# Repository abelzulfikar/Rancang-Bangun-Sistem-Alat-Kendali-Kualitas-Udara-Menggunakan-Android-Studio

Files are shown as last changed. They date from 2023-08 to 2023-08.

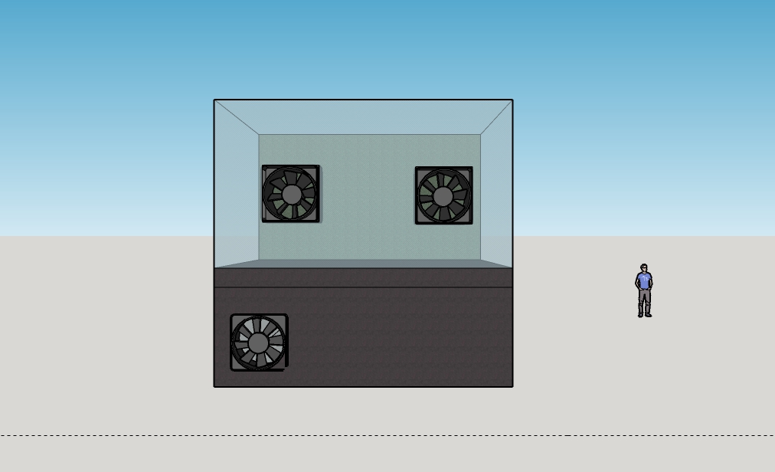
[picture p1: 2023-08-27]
Pendukung/SketchUp/bagian 2 tampilan belakang.jpg

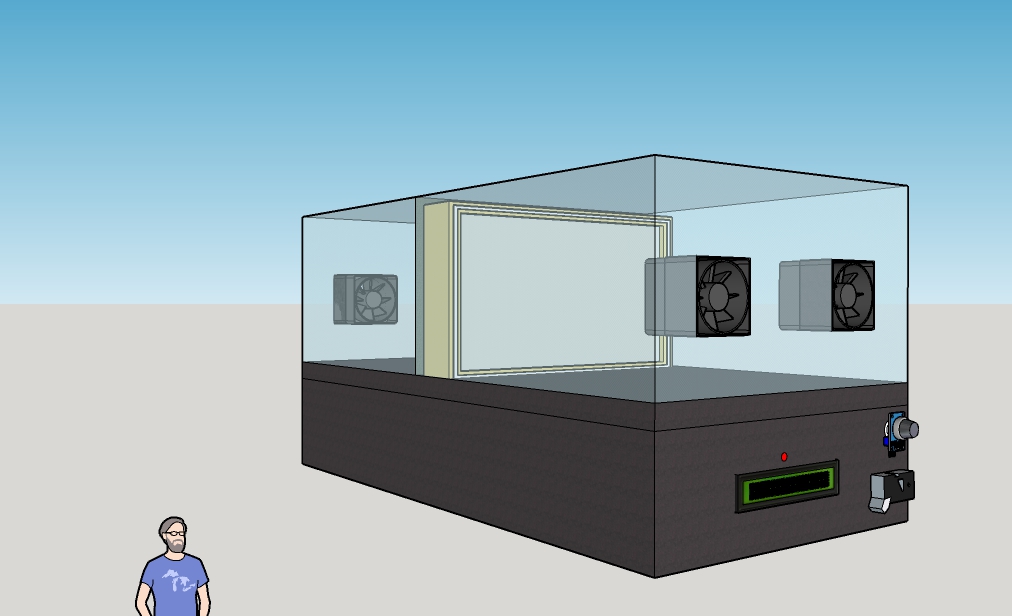
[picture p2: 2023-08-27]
Pendukung/SketchUp/bagian 2 tampilan samping 2.jpg

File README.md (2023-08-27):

# Rancang-Bangun-Sistem-Alat-Kendali-Kualitas-Udara-Menggunakan-Android-Studio
memantau dan mengatur kualitas udara dalam ruangan melalui aplikasi Android

Latar Belakang
Kualitas udara dalam ruangan memiliki dampak besar pada kesehatan dan kenyamanan manusia sehari-hari. Udara yang tercemar dapat menyebabkan gangguan pernapasan, alergi, dan dampak negatif lainnya. Karena banyaknya waktu yang dihabiskan di dalam ruangan, baik di tempat tinggal maupun tempat kerja, pengendalian kualitas udara menjadi penting. Diperlukan alat Sistem Kendali Kualitas Udara dengan sensor MQ 135 untuk mendeteksi udara tidak sehat, sensor GP2Y1010AU0F untuk sensitivitas debu, dan penambahan filter H13 atau HEPA untuk menyaring udara dari kotoran

Menghubungkan alat melalui socket AC ke sumber listrik.
1. Menghubungkan ESP 32 dengan jaringan Wi-Fi yang memiliki akses internet
2. Buka aplikasi "Freshism" yang sudah diinstal pada smartphone
3. Sensor akan membaca nilai udara dan debu dan hasilnya akan tampil di aplikasi
4. Tekan Tombol ON untuk mengaktifkan Kipas DC
5. Pilih Mode "Auto" pada tombol aplikasi "Freshism"
6. jika indikator kualitas udara tidak sehat, maka indikator led akan berwarna merah, tampilan aplikasi tidak sehat, dan kipas dc menyala

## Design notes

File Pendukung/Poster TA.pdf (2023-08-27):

PERALATAN

LATAR BELAKANG

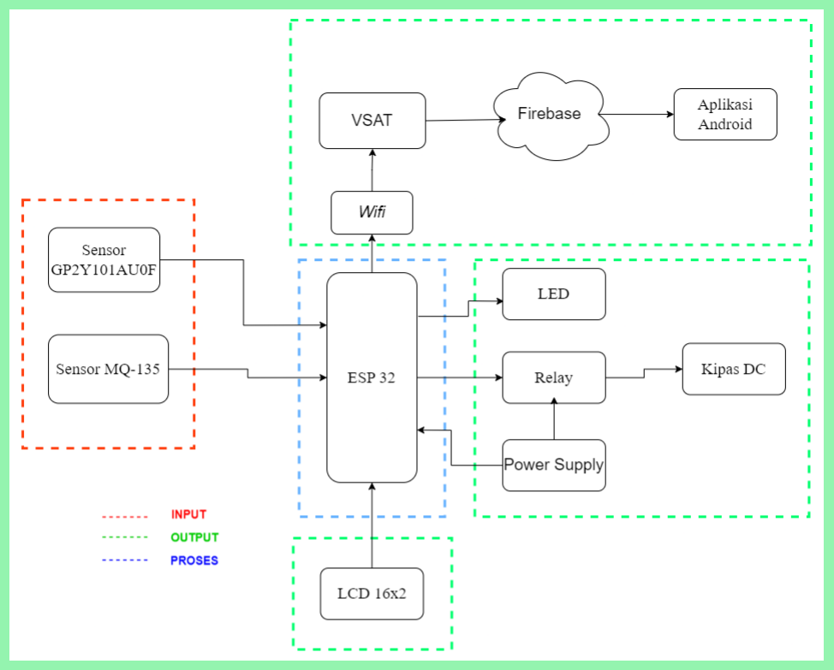
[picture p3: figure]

Rosnabila Enggar Pawening
2003332064

Pembimbing: Dita Indra Febriyanti S.Pd., M.Han NIP: 199402022022032015

NAMA MAHASISWA 2

Zulfikar Bella Ali
NIM: 2003332007

Pembimbing: Ir. Sri Danaryani., M.T. NIP: 196305031991032001

NAMA MAHASISWA 1

TUJUAN

DIAGRAM BLOK

KEMENTRIAN RISET, TEKNOLOGI, DAN PENDIDIKAN TINGGI POLITEKNIK NEGERI JAKARTA
JURUSAN TEKNIK ELEKTRO
Jl. Prof. DR. G.A. Siwabessy, Kampus UI, Depok 16425 Telp/Fax Elektro: ( 021 ) 7863531, ( 021 ) 7270036 Hunting Laman: http://www.pnj.ac.id, e-mail: elektro@pnj.ac.id

## RANCANG BANGUN SISTEM KENDALI KUALITAS UDARA MENGGUNAKAN APLIKASI ANDROID

ESP 32
Sensor MQ-135
Sensor GP2Y1010AU0F
LED RGB
Relay dua channel
LCD 16x2
Kipas DC
Power Supply

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
Kualitas udara dalam ruangan memiliki dampak besar pada kesehatan dan kenyamanan manusia
sehari-hari. | Udara | yang | tercemar | dapat
menyebabkan gangguan pernapasan, alergi, dan dampak negatif lainnya. Karena banyaknya waktu yang dihabiskan di dalam ruangan, baik di tempat tinggal maupun tempat kerja, pengendalian kualitas udara menjadi penting. Diperlukan alat Sistem Kendali Kualitas Udara dengan sensor MQ 135 untuk mendeteksi udara tidak sehat, sensor GP2Y1010AU0F untuk sensitivitas debu, dan penambahan filter H13 atau HEPA untuk menyaring udara dari kotoran

Mampu merancang catu daya dari sistem kendali kualitas udara menggunakan aplikasi Mampu untuk melakukan perancangan sistem untuk kendali kualitas udara
Mampu melakukan pengujian komponen dan pembacaan data kualitas udara dari alat kendali kualitas udara menggunakan aplikasi Mampu merancang aplikasi android sistem kendali kualitas udara.
Mampu untuk melakukan pengintergrasian antara alat sistem kendali kualitas udara dan aplikasi melalui data firebase
Mampu melakukan pengujian pembacaan data dari alat ke aplikasi

1.

2.

3.

4.

5.

6.

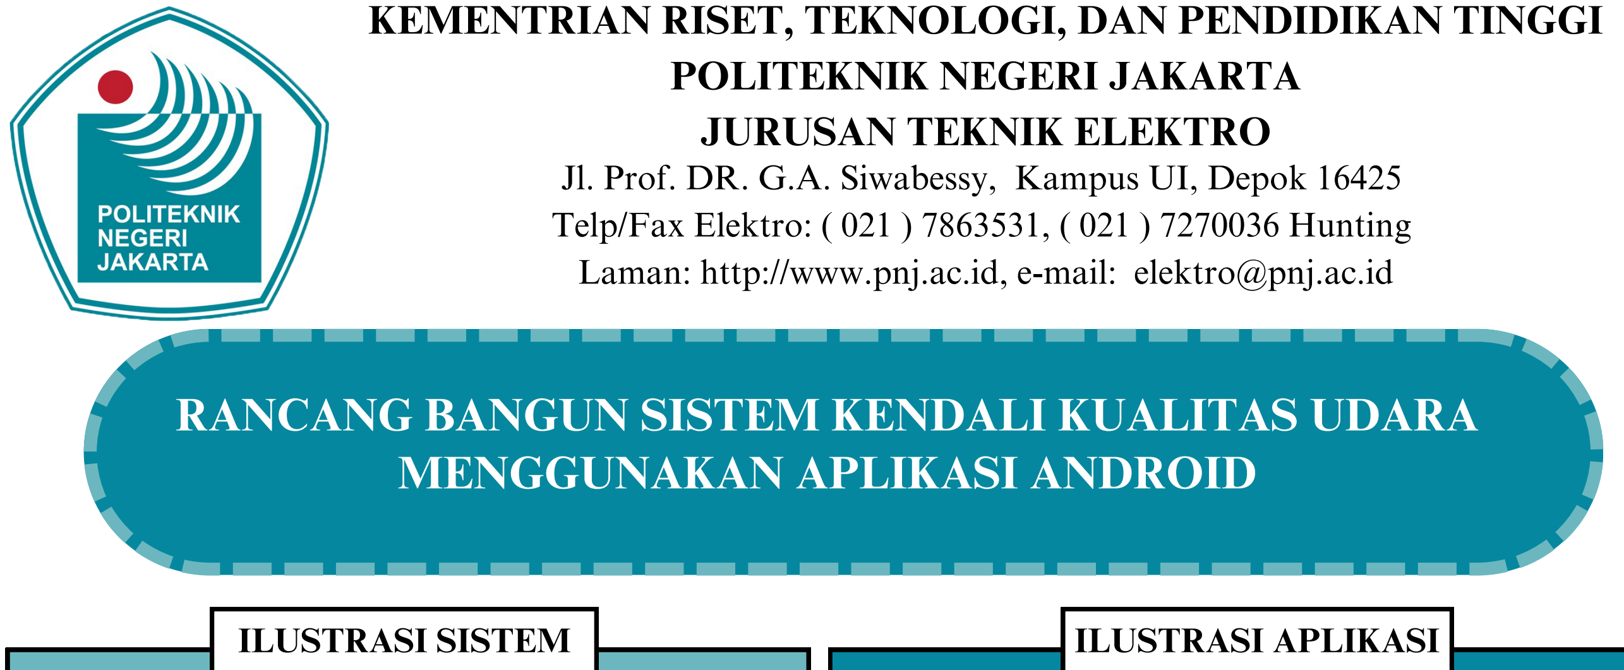
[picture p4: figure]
ILUSTRASI SISTEM; ILUSTRASI APLIKASI; POLITEKNIK NEGERI JAKARTA JURUSAN TEKNIK ELEKTRO; Laman: http://www.pnj.ac.id, e-mail: elektro@pnj.ac.id; MENGGUNAKAN APLIKASI ANDROID
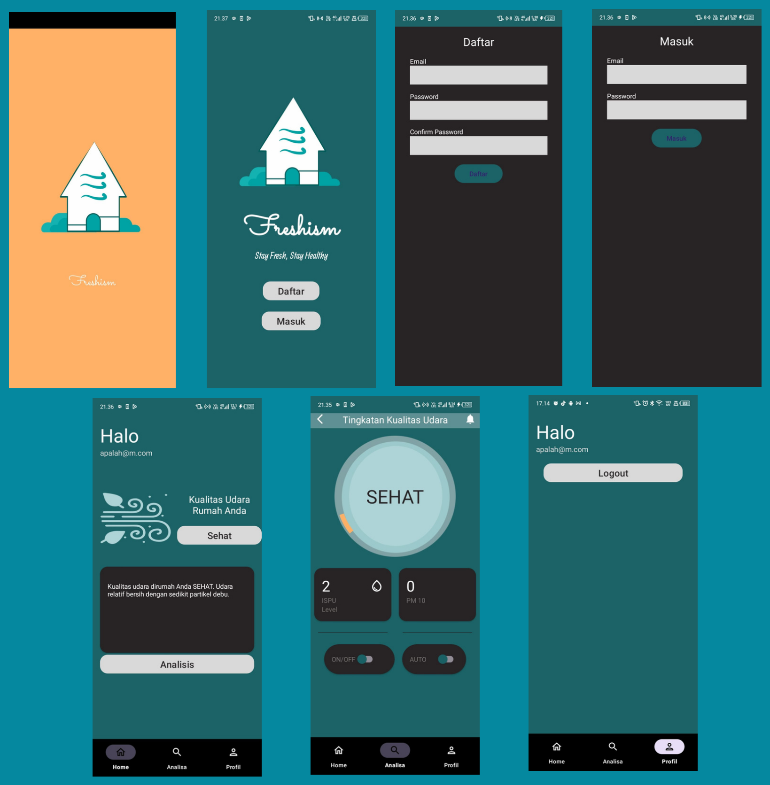
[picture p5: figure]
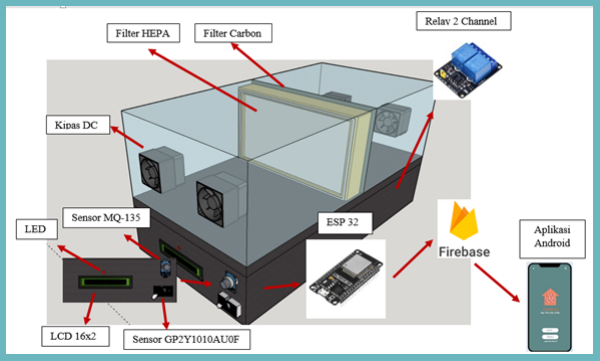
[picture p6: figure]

CARA PENGOPERASIAN ALAT

Rosnabila Enggar Pawening
NIM: 2003332064

Pembimbing: Dita Indra Febriyanti S.Pd., M.Han NIP: 199402022022032015

NAMA MAHASISWA 2

Zulfikar Bella Ali
NIM: 2003332007

Pembimbing: Ir. Sri Danaryani., M.T. NIP: 196305031991032001

NAMA MAHASISWA 1

KEMENTRIAN RISET, TEKNOLOGI, DAN PENDIDIKAN TINGGI

Jl. Prof. DR. G.A. Siwabessy, Kampus UI, Depok 16425 Telp/Fax Elektro: ( 021 ) 7863531, ( 021 ) 7270036 Hunting

## RANCANG BANGUN SISTEM KENDALI KUALITAS UDARA

Menghubungkan alat melalui socket AC ke sumber listrik.
Menghubungkan ESP 32 dengan jaringan Wi-Fi yang memiliki akses internet Buka aplikasi "Freshism" yang sudah diinstal pada smartphone
Sensor akan membaca nilai udara dan debu dan hasilnya akan tampil di aplikasi
Tekan Tombol ON untuk mengaktifkan Kipas DC
Pilih Mode "Auto" pada tombol aplikasi "Freshism"
jika indikator kualitas udara tidak sehat, maka indikator led akan berwarna merah, tampilan aplikasi tidak sehat, dan kipas dc menyala

1.
2.
3.
4.
5.
6.
7.

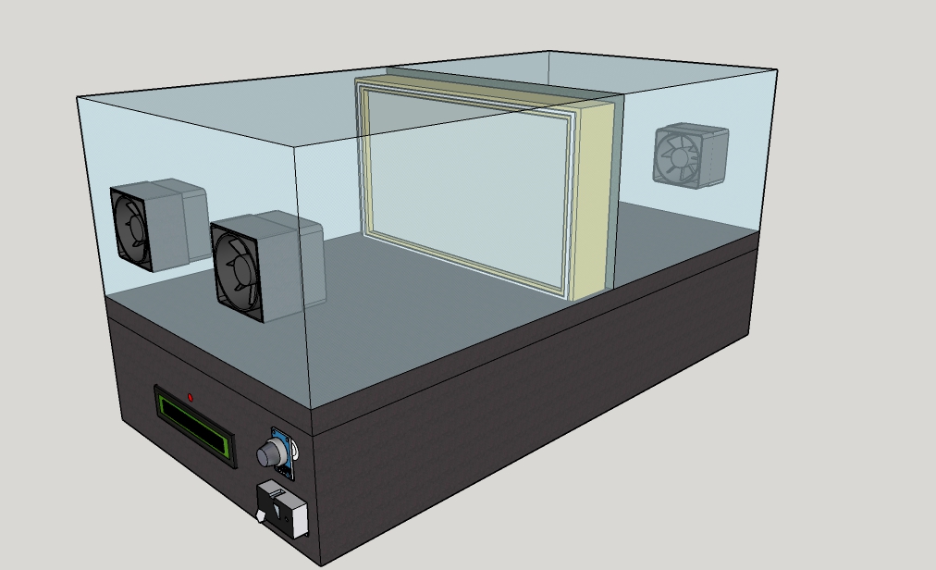
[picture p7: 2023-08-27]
Pendukung/SketchUp/bagian 2 tampilan samping.jpg

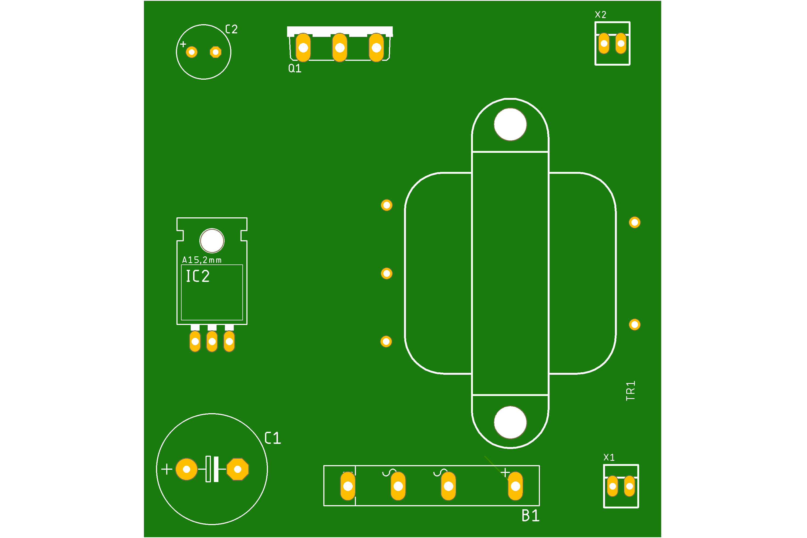
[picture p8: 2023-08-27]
Pendukung/Eagle/Power Supply untuk IC Regulator/Final.png

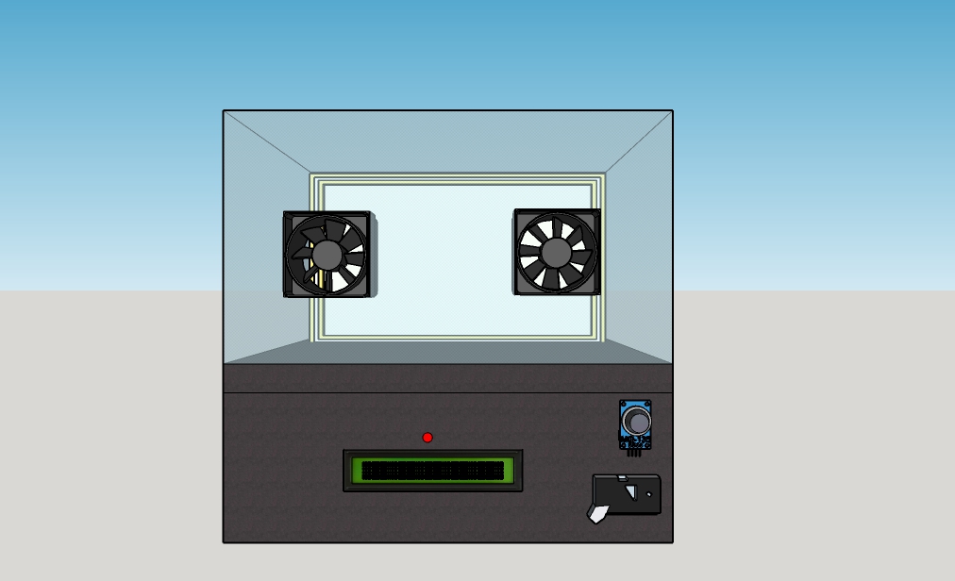
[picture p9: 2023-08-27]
Pendukung/SketchUp/bagian 2 tampilan depan.jpg

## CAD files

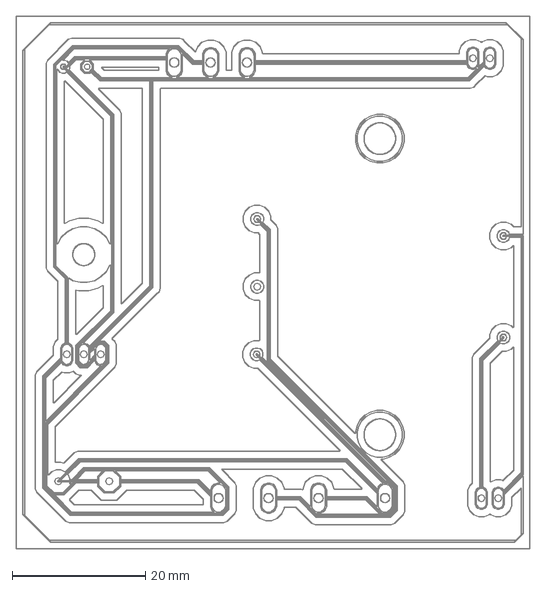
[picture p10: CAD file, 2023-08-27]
Pendukung/Eagle/Power Supply untuk IC Regulator/Final.dxf
77.1 x 80.0 mm

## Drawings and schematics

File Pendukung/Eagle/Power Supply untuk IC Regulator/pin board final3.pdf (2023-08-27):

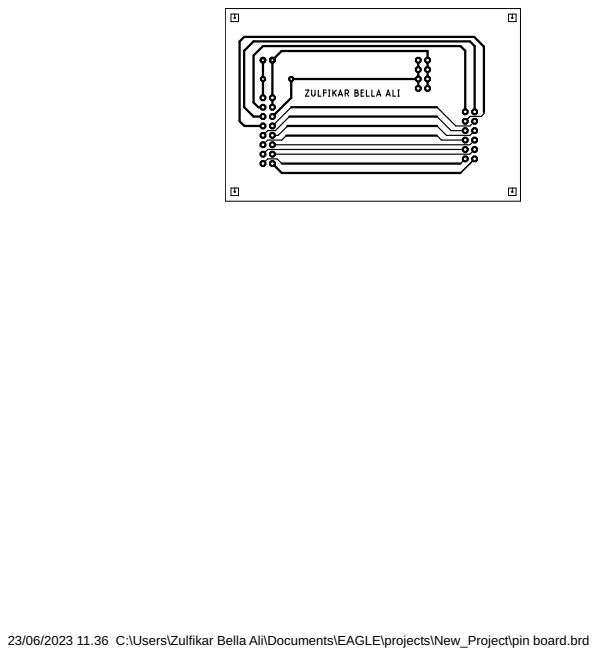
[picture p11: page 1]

23/06/2023 11.36 C:\Users\Zulfikar Bella Ali\Documents\EAGLE\projects\New_Project\pin board.brd

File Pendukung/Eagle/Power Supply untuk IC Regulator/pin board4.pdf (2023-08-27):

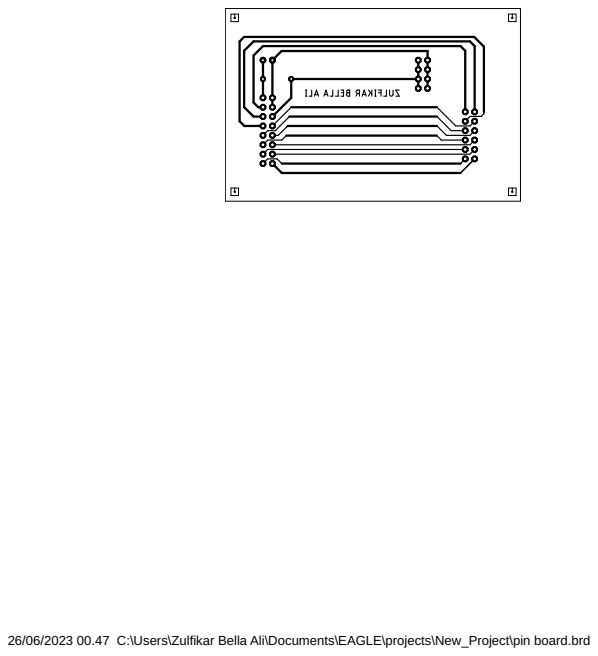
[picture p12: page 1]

26/06/2023 00.47 C:\Users\Zulfikar Bella Ali\Documents\EAGLE\projects\New_Project\pin board.brd

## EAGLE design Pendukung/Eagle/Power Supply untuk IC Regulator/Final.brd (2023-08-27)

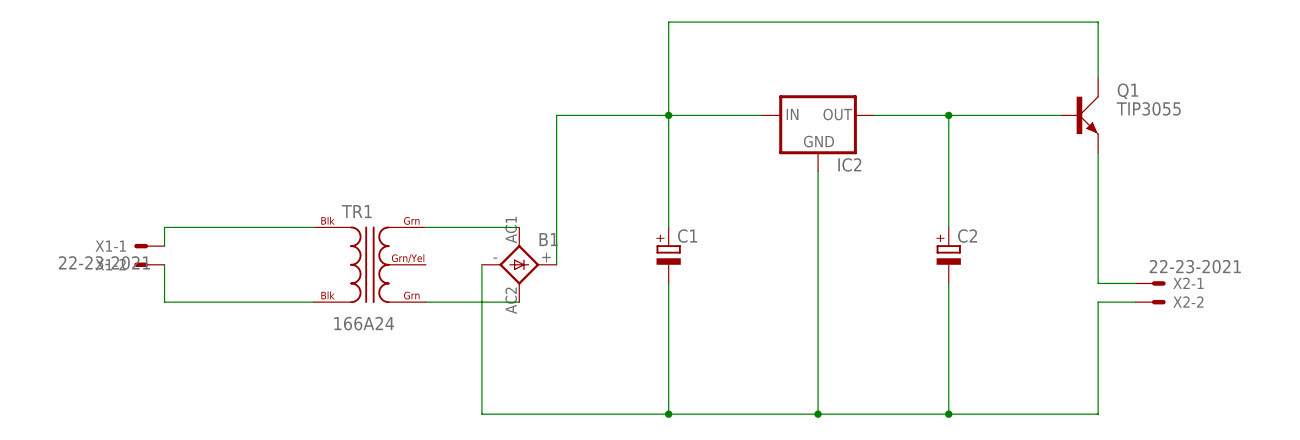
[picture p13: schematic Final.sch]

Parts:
B1: FB32
C1: CPOL-EUE7.5-16; E7,5-16
C2: CPOL-EUE3.5-8; E3,5-8
IC2: 78XXL
Q1: TIP3055; TOP3AV
TR1: 166A24; C2H
X1, X2: 22-23-2021

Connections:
unnamed: TR1.BLK@1 (BLK), X1.1
unnamed: TR1.BLK@2 (BLK), X1.2
unnamed: B1.AC1, TR1.GRN@1 (GRN)
unnamed: B1.AC2, TR1.GRN@2 (GRN)
unnamed: B1.+, C1.+, IC2.IN, Q1.C
unnamed: B1.-, C1.-, C2.-, IC2.GND, X2.2
unnamed: Q1.E, X2.1
unnamed: C2.+, IC2.OUT, Q1.B

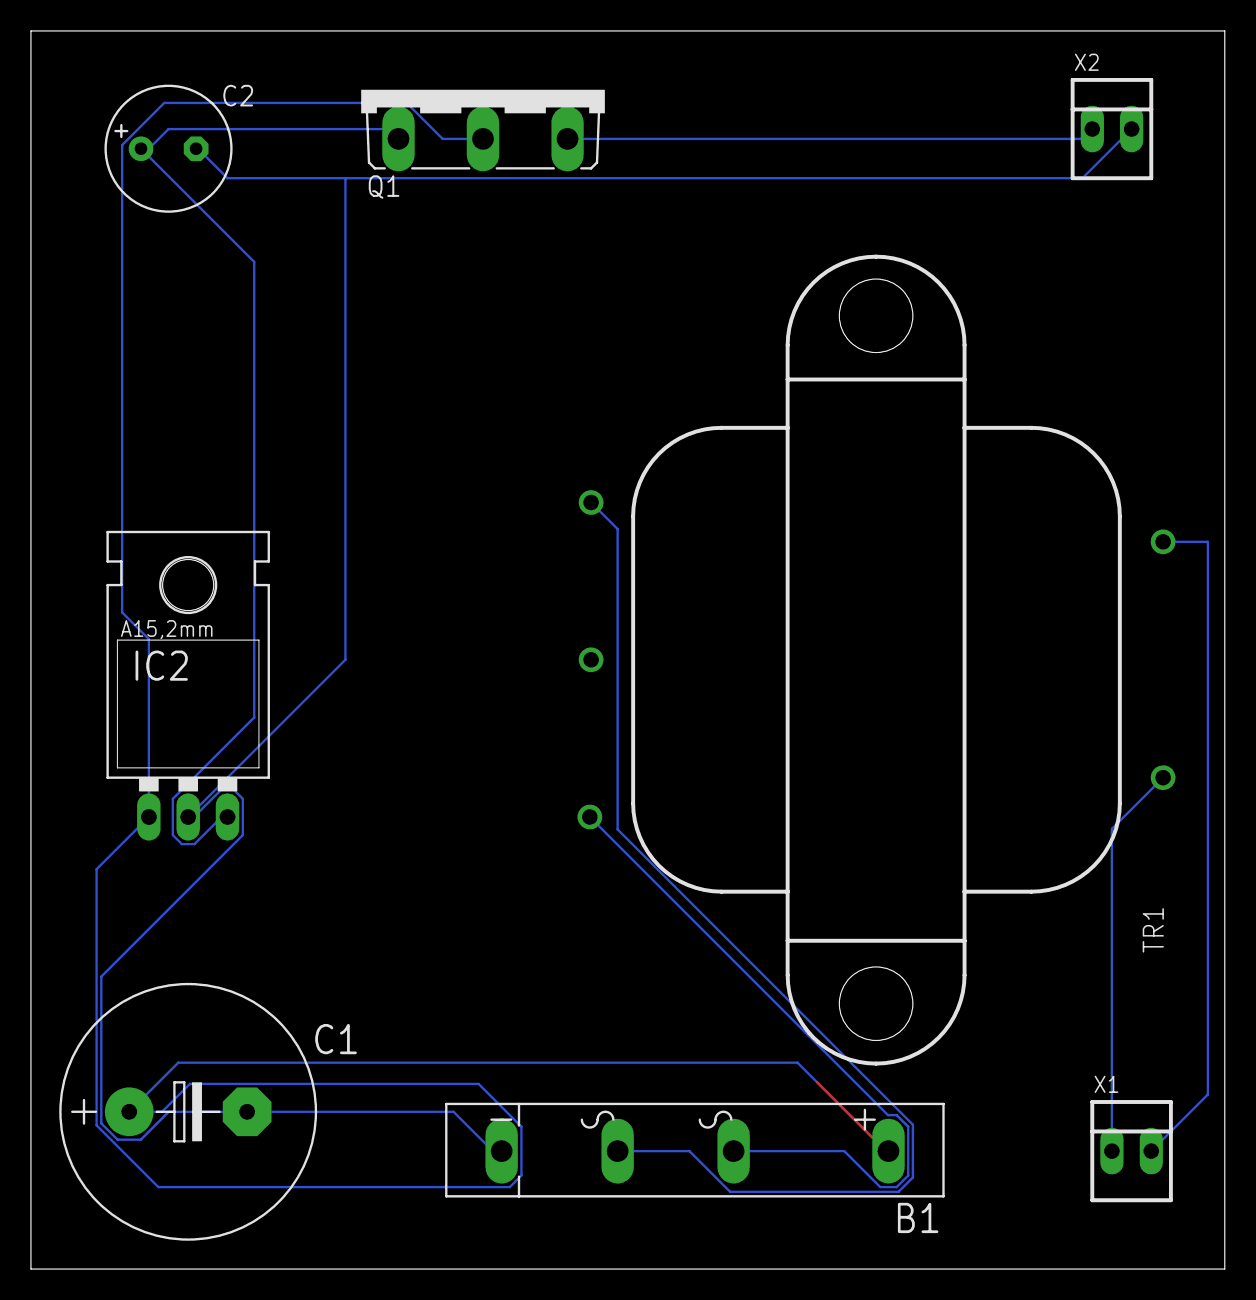
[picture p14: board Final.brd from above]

Board: 2 copper layers, 77.1 x 80.0 mm, 8 parts (0 on the bottom side), 8 nets.

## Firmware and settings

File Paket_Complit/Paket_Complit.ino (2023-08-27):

//Include the library
#include <MQUnifiedsensor.h>
#include <LiquidCrystal_I2C.h>
#include <Wire.h>

//Definitions
#define placa "ESP-32"
#define Voltage_Resolution 3.3
#define pin 35 //Analog input 0 of your arduino
#define type "MQ-135" //MQ135
#define ADC_Bit_Resolution 12 // For ESP32
#define RatioMQ135CleanAir 3.6//RS / R0 = 3.6 ppm  

const int pinGP2Y = 34;
int pinLED = 27;
int samplingTime = 280;
int deltaTime = 40;
int sleepTime = 9680;

//Declare Sensor
MQUnifiedsensor MQ135(placa, Voltage_Resolution, ADC_Bit_Resolution, pin, type);

char jenisgas[6][10] = {"CO","Alcohol","CO2","Toluen","NH4","Aceton"};
float gasA [6] = {605.18 , 77.255 , 110.47 , 44.947 , 102.2 , 34.668};
float gasB [10] = {-3.937 , -3.18 , -2.862 , -3.445 , -2.473 , -3.369};
int CO = 0;

#define relaypin 5
 
LiquidCrystal_I2C lcd(0x27,16,2);
 

 
byte pic_termo[8] = //icon for termometer
{
  B00000,
  B00000,
  B00000,
  B00000,
  B00000,
  B11111,
  B11111,
  B00000
};
 
byte pic_humd[8] = //icon for water droplet
{
    B00000,
  B00010,
  B00101,
  B01000,
  B10100,
  B00010,
  B00101,
  B00000
};
 
byte lonceng[8] = {
  B00100,
  B01110,
  B01110,
  B01110,
  B11111,
  B00000,
  B00100,
  B00000
};
 
byte lonceng1[8] = {
  B11011,
  B10001,
  B10001,
  B10001,
  B10001,
  B00000,
  B11111,
  B11011
};

void setup() {
  //Init the serial port communication - to debug the library
  Serial.begin(115200); //Init serial port
  pinMode(relaypin, OUTPUT);
  pinMode(pinLED,OUTPUT);
  
  //Set math model to calculate the PPM concentration and the value of constants
  MQ135.setRegressionMethod(1); //_PPM =  a*ratio^b
  MQ135.setA(gasA[CO]); MQ135.setB(gasB[CO]); // Configure the equation to to calculate CO concentration
  /*
    Exponential regression:
  GAS      | a      | b
  CO       | 605.18 | -3.937  
  Alcohol  | 77.255 | -3.18 
  CO2      | 110.47 | -2.862
  Toluen  | 44.947 | -3.445
  NH4      | 102.2  | -2.473
  Aceton  | 34.668 | -3.369
  */
  
  /*****************************  MQ Init ********************************************/ 
  //Remarks: Configure the pin of arduino as input.
  /************************************************************************************/ 
  MQ135.init(); 
  /* 
    //If the RL value is different from 10K please assign your RL value with the following method:
    MQ135.setRL(10);
  */
  /*****************************  MQ CAlibration ********************************************/ 
  // Explanation: 
   // In this routine the sensor will measure the resistance of the sensor supposedly before being pre-heated
  // and on clean air (Calibration conditions), setting up R0 value.
  // We recomend executing this routine only on setup in laboratory conditions.
  // This routine does not need to be executed on each restart, you can load your R0 value from eeprom.
  // Acknowledgements: https://jayconsystems.com/blog/understanding-a-gas-sensor
  Serial.print("Calibrating please wait.");
  float calcR0 = 0;
  for(int i = 1; i<=10; i ++)
  {
    MQ135.update(); // Update data, the arduino will read the voltage from the analog pin
    calcR0 += MQ135.calibrate(RatioMQ135CleanAir);
    Serial.print(".");
  }
  MQ135.setR0(calcR0/10);
  Serial.println("  done!.");
  
  if(isinf(calcR0)) {Serial.println("Warning: Conection issue, R0 is infinite (Open circuit detected) please check your wiring and supply"); while(1);}
  if(calcR0 == 0){Serial.println("Warning: Conection issue found, R0 is zero (Analog pin shorts to ground) please check your wiring and supply"); while(1);}
  /*****************************  MQ CAlibration ********************************************/ 
  MQ135.serialDebug(false);


  
  lcd.begin();
  lcd.setBacklight(255);
  lcd.setCursor(00,00);
  lcd.print("Kendali Kualitas");
  lcd.setCursor(00,1);
  lcd.print("     Udara ");
  delay(1000);
  lcd.clear();
  lcd.setCursor(00,00);
  lcd.print("Zulfikar Bella A");
  lcd.setCursor(00,1);
  lcd.print("Rosnabila Enggar");
  delay(2000);
  lcd.clear();
  lcd.createChar(1,pic_termo);
  lcd.createChar(2,pic_humd);
  lcd.createChar(3,lonceng);
  lcd.createChar(4,lonceng1);
}

void loop() {
  delay(1000);
  MQ135.update(); // Update data, the arduino will read the voltage from the analog pin
  float Udara = MQ135.readSensor(); // Sensor will read PPM concentration using the model, a and b values set previously or from the setup

  Serial.print(jenisgas[CO]);Serial.print (" : ");Serial.print(Udara);Serial.println(" ppm");
  MQ135.serialDebug(); // Will print the table on the serial port
  MQ135.init(); 

  digitalWrite(pinLED,LOW); // Turn On the LED
  delayMicroseconds(samplingTime);
  
  float voMeasured = analogRead(pinGP2Y); // Read the dust value
  delayMicroseconds(deltaTime);
  
  digitalWrite(pinLED,HIGH); // Turn Off the LED
  delayMicroseconds(sleepTime);
  
  float calcVoltage = voMeasured * (3.3/4096);
  // linear equation taken from http://www.howmuchsnow.com/arduino/airquality/
  // Chris Nafis (c) 2012
  float dustDensity = (0.17 * calcVoltage - 0.1)*1000;
  if (dustDensity < 0){
    dustDensity = 0;
  }
  Serial.print("Raw signal value (0-4045): "); Serial.print(voMeasured);
  Serial.print(" - Voltage: "); Serial.print(calcVoltage);
  Serial.print(" - Density : "); Serial.println(dustDensity);



  lcd.setCursor (00,00);
  lcd.print("UDARA  &  DEBU");
  lcd.setCursor (00,1);
  lcd.write(1);
  lcd.setCursor (1,1);
  lcd.print(Udara);

  lcd.setCursor (5,1);
  lcd.print("       ");
  lcd.setCursor (14,1);
  lcd.print("  ");
  
  lcd.setCursor (9,1);
  lcd.write(2);
  lcd.setCursor (10,1);
  lcd.print(dustDensity);

  if (Udara >= 101 ){
    lcd.clear();
    while(1){
      // Menghitung Level AQI berdasarkan nilai ppm CO2
      MQ135.setRegressionMethod(1); //_PPM =  a*ratio^b
      MQ135.setA(605.18); MQ135.setB(-3.937);
      MQ135.update(); // Update data, the arduino will read the voltage from the analog pin
  float DataUdara = MQ135.readSensor(); // Sensor will read PPM concentration using the model, a and b values set previously or from the setup

      digitalWrite(relaypin, HIGH); 
      delay(3000);
      lcd.setCursor (00,00);
      lcd.write(1);
      lcd.print(" Tidak Sehat");
      
      lcd.setCursor (1,1);
      lcd.print(DataUdara);
      lcd.setCursor (5,1);
      lcd.print("      ");
      lcd.setCursor (9,1);
      lcd.print("FAN ON");
      
      lcd.setCursor (8,1);
      lcd.write(3);
      delay(2000);
      lcd.setCursor (8,1);
      lcd.write(4);
      delay(2000);
 
      
      if (DataUdara <= 100) {
        digitalWrite(relaypin, LOW); 
        lcd.clear();
        break;
        }
    }
  }

  if (dustDensity >= 101 ){
    lcd.clear();
    while(1){
digitalWrite(relaypin, HIGH);
  digitalWrite(pinLED,LOW); // Turn On the LED
  delayMicroseconds(280);
  
  float voMeasured = analogRead(pinGP2Y); // Read the dust value
  delayMicroseconds(40);
  
  digitalWrite(pinLED,HIGH); // Turn Off the LED
  delayMicroseconds(9680);
  
  float calcVoltage = voMeasured * (3.3/4096);
  // linear equation taken from http://www.howmuchsnow.com/arduino/airquality/
  // Chris Nafis (c) 2012
  float dustDensity = (0.17 * calcVoltage - 0.1)*1000;
  if (dustDensity < 0){
    dustDensity = 0;
  }
      
      lcd.setCursor (00,00);
      lcd.write(2);
      lcd.print(" Tidak Sehat");
      lcd.setCursor (00,1);
      
      lcd.setCursor (1,1);
      lcd.print(dustDensity);
      lcd.setCursor (5,1);
      lcd.print("      ");
      lcd.setCursor (9,1);
      lcd.print("FAN ON");
      
      lcd.setCursor (8,1);
      lcd.write(3);

      lcd.setCursor (8,1);
      lcd.write(4);
      delay(2000);
 
       
      
      if (dustDensity <= 100) {
        digitalWrite(relaypin, LOW); 
        lcd.clear();
        break;
        }
    }
  }

}
